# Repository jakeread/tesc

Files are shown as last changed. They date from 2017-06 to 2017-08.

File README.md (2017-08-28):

# FOCT v0.3
### Field Oriented Control on a Teensy 3.2

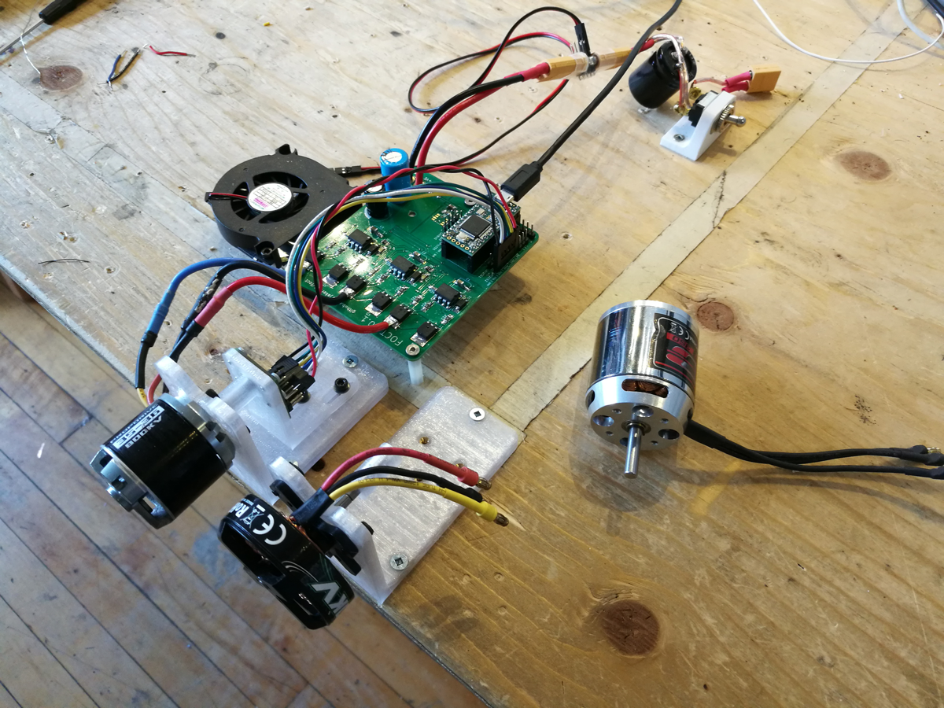
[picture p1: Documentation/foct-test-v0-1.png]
FOCT System


## Briefly
FOCT does closed-loop control of brushless dc (BLDC) motors: the type normally found in RC Cars, Airplanes, Drones etc. These motors are incredibly power-dense, making them an excellent candidate for Robotics applications. However, it's very difficult to control them at low speeds and in small position intervals. 

FOCT implements 'all the bells and whistles' found in high-end robotics motor controllers (encoder feedback, BEMF & current sensing, etc) in a relatively low-cost solution. Code is written in Arduino for the Teensy Microcontroller, and is meant to be easily extensible and pick-through-able.

FOCT is in development! So is it's documentation!

## The Hardware  
FOCT uses a Teensy 3.2 to control Three H-Bridges, which each drive one phase of a three-phase brushless motor. The H-Bridge gates are driven with a DRV8302, a wunderkid IC that is also home to a 5V Buck Converter (for your peripheral needs) and two differential Op-Amps, used to measure phase current. The board also has simple voltage-dividers connected to Teensy ADCs for measuring phase voltage, and includes an SPI out connector used to interface with an AS5047 encoder for absolute position sensing. For now, input is done over Teensy's blazing-fast serial port.  
  
Up to ~24v supply  
Up to 30A without a heatsink, 42 with good cooling, peaks of 60  
Planned PWM in, SPI slave modes for control. Serial over USB Config / testing.  

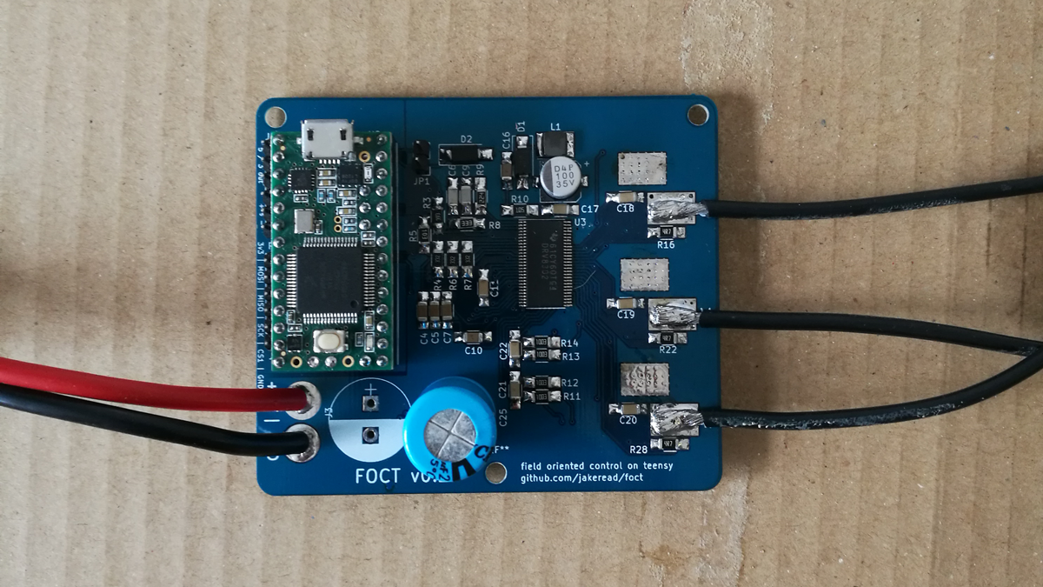
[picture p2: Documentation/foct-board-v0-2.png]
FOCT v0.2 Hardware


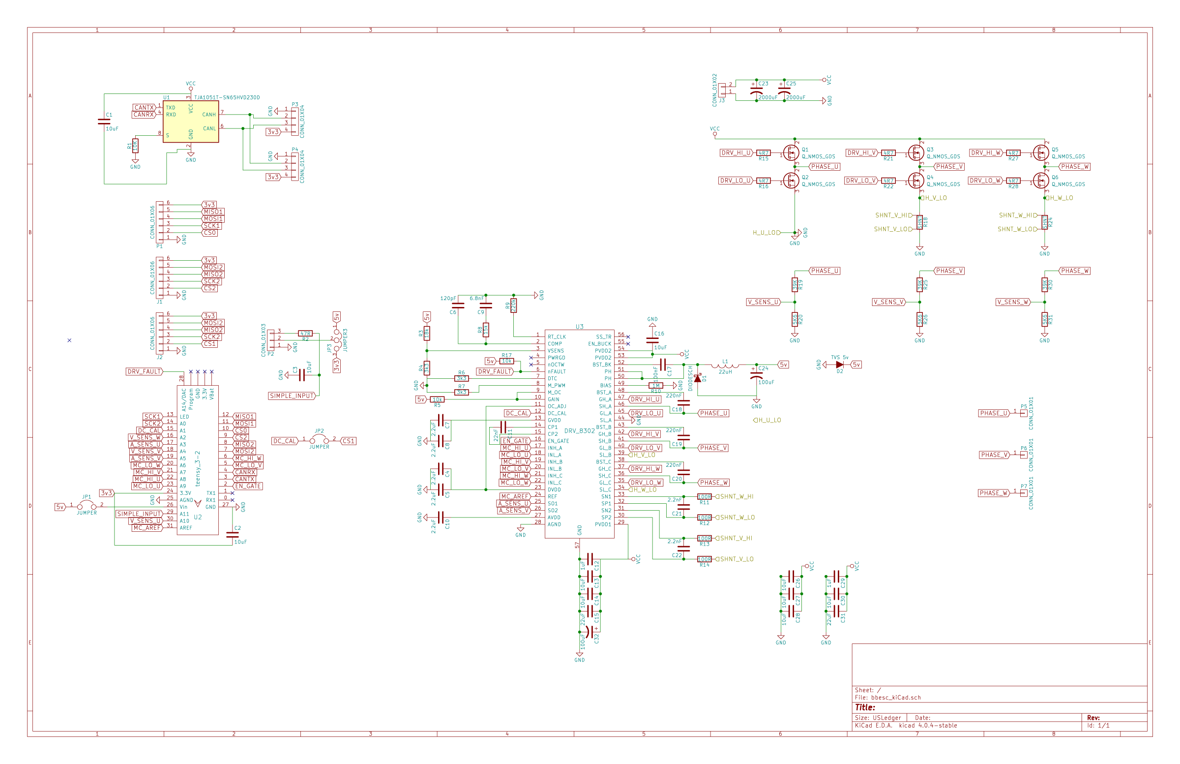
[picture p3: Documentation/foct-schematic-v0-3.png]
FOCT v0.3 Schematic


## The Software
FOCT runs on Arduino! It uses Teensy's built interval timers to handle fast-loop-insurance, and only occasionally reaches into the chip's registers to make PWM work properly. Code will be well commented, I hope / promise...

## How it Works: Closed-Loop BLDC Control
// 6-step commutation w/ position reference

## How it Works: Field-Oriented Control
// FOC ! Transforms, current measurement, UVW || AB || IQ frames  

## TBD's, software
- Proper filtering on Current measurement, encoder measurement  
- Tuning the FOC loop  
- Encoder Offset Discovery routine  
- Auto Tuning, interface, system integration, oh my

## TBD's, hardware
- ADC voltage divider to sense VBUS voltage
- More DAC outputs / testing pins so to tune FOC
- SMD Thermistor near the FETS ?  
- Go to STM32F4 & chibios ?
- Caps could be closer to FETS, heatsink strap

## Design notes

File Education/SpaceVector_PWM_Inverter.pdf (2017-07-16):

## PROJECT #2 SPACE VECTOR PWM INVERTER

JIN-WOO JUNG, PH.D STUDENT

E-mail: jung.103@osu.edu
Tel.: (614) 292-3633

ADVISOR: PROF. ALI KEYHANI

## DATE: FEBRUARY 20, 2005

### MECHATRONIC SYSTEMS LABORATORY

### DEPARTMENT OF ELECTRICAL AND COMPUTER ENGINEERING

### THE OHIO STATE UNIVERSITY

### 1. Problem Description

In this simulation, we will study Space Vector Pulse Width Modulation (SVPWM) technique. We will use the SEMIKRON® IGBT Flexible Power Converter for this purpose. The system configuration is given below:

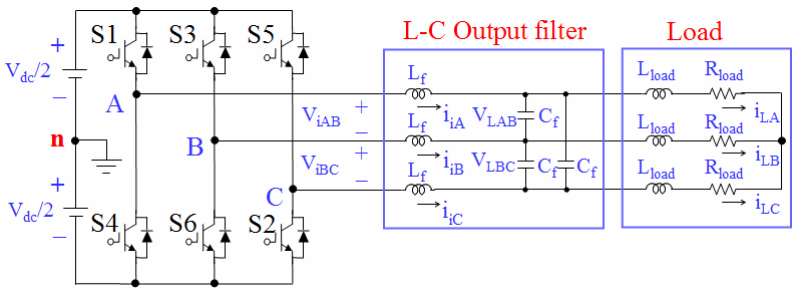
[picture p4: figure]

Fig. 1 Circuit model of three-phase PWM inverter with a center-taped grounded DC bus.

The system parameters for this converter are as follows:

IGBTs: SEMIKRON SKM 50 GB 123D, Max ratings: VCES = 600 V, IC = 80 A DC- link voltage: Vdc = 400 V
Fundamental frequency: f = 60 Hz
PWM (carrier) frequency: fz = 3 kHz
Modulation index: a = 0.6
Output filter: Lf = 800 µH and Cf = 400 µF
Load: Lload = 2 mH and Rload = 5 Ω

Using Matlab/Simulink, simulate the circuit model described in Fig. 1 and plot the waveforms of Vi (= [ViAB ViBC ViCA]), Ii (= [iiA iiB iiC]), VL (= [VLAB VLBC VLCA]), and IL (= [iLA iLB iLC]).

### 2. Space Vector PWM

### 2.1 Principle of Pulse Width Modulation (PWM)

Fig. 2 shows circuit model of a single-phase inverter with a center-taped grounded DC bus, and Fig 3 illustrates principle of pulse width modulation.

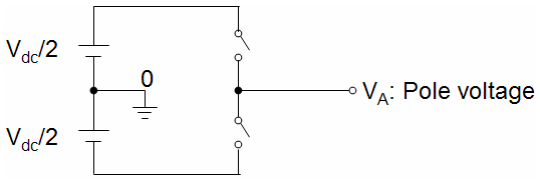
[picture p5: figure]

Fig. 2 Circuit model of a single-phase inverter.

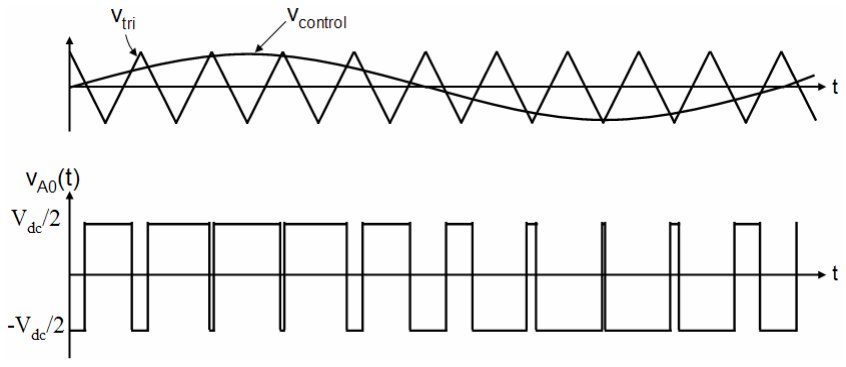
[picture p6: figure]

Fig. 3 Pulse width modulation.

As depicted in Fig. 3, the inverter output voltage is determined in the following: When Vcontrol > Vtri, VA0 = Vdc/2
When Vcontrol < Vtri, VA0 = −Vdc/2

Also, the inverter output voltage has the following features:
PWM frequency is the same as the frequency of Vtri
Amplitude is controlled by the peak value of Vcontrol
Fundamental frequency is controlled by the frequency of Vcontrol

Modulation index (m) is defined as:

A0 1 | A0 0 1

where, (V ) : fundamental frequecny component of V

, / 2

( )

dc

A

tri

control
V

peak of V
v

v
∴m = =

### 2.2 Principle of Space Vector PWM

The circuit model of a typical three-phase voltage source PWM inverter is shown in Fig. 4. S1 to S6 are the six power switches that shape the output, which are controlled by the switching variables a, a′, b, b′, c and c′. When an upper transistor is switched on, i.e., when a, b or c is 1, the corresponding lower transistor is switched off, i.e., the corresponding a′, b′ or c′ is 0. Therefore, the on and off states of the upper transistors S1, S3 and S5 can be used to determine the output voltage.

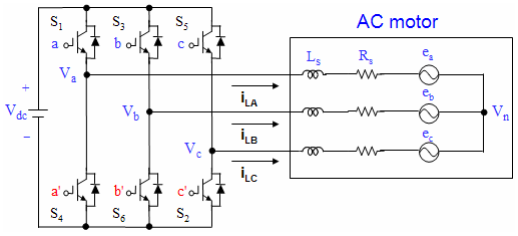
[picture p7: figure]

Fig. 4 Three-phase voltage source PWM Inverter.

The relationship between the switching variable vector [a, b, c]t and the line-to-line voltage vector [Vab Vbc Vca]

t
is given by (2.1) in the following:

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
1 0 | 1
0 | 1 | 1
1 | 1 0
. | (2.1)

Also, the relationship between the switching variable vector [a, b, c]t and the phase voltage
vector [Va Vb Vc]

t
can be expressed below.

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
− − − −
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
1 | 1 2
1 2 | 1
2 | 1 | 1
3 | . | (2.2)

As illustrated in Fig. 4, there are eight possible combinations of on and off patterns for the three upper power switches. The on and off states of the lower power devices are opposite to the upper one and so are easily determined once the states of the upper power transistors are determined. According to equations (2.1) and (2.2), the eight switching vectors, output line to neutral voltage (phase voltage), and output line-to-line voltages in terms of DC-link Vdc, are given in Table1 and Fig. 5 shows the eight inverter voltage vectors (V0 to V7).

Table 1. Switching vectors, phase voltages and output line to line voltages

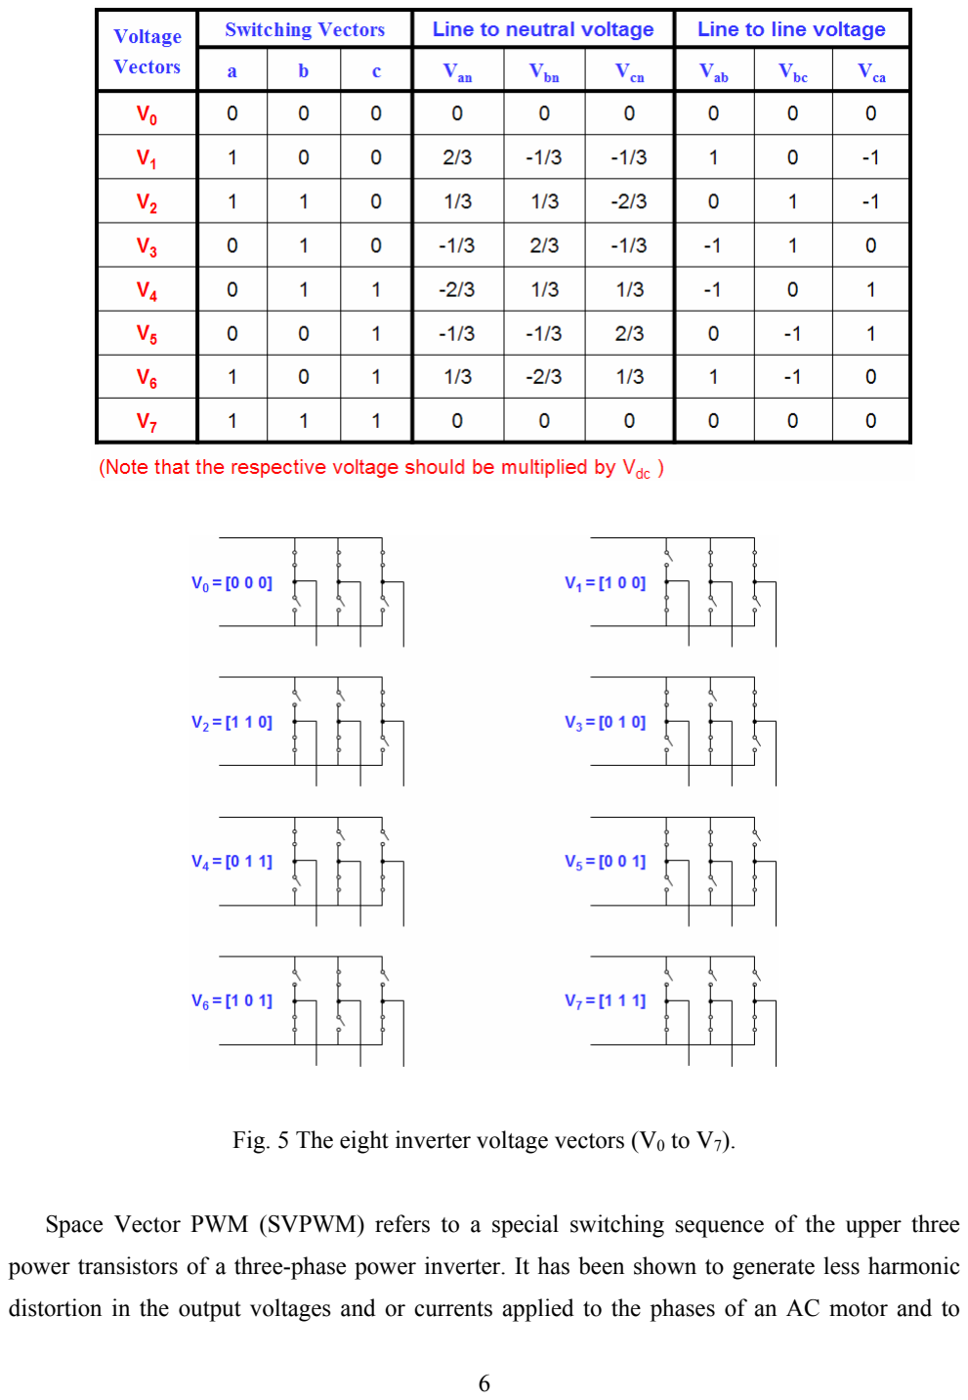
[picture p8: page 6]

Fig. 5 The eight inverter voltage vectors (V0 to V7).

Space Vector PWM (SVPWM) refers to a special switching sequence of the upper three power transistors of a three-phase power inverter. It has been shown to generate less harmonic distortion in the output voltages and or currents applied to the phases of an AC motor and to provide more efficient use of supply voltage compared with sinusoidal modulation technique as shown in Fig. 6.

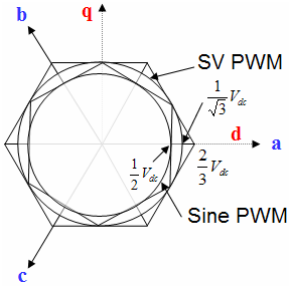
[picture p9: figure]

Fig. 6 Locus comparison of maximum linear control voltage in Sine PWM and SVPWM.

To implement the space vector PWM, the voltage equations in the abc reference frame

can be transformed into the stationary dq reference frame that consists of the horizontal (d) and

vertical (q) axes as depicted in Fig. 7.

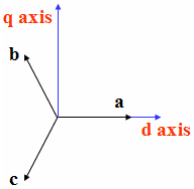
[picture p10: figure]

Fig. 7 The relationship of abc reference frame and stationary dq reference frame.

From this figure, the relation between these two reference frames is below

dq | s abc f | = K f 0 | (2.3)

where,
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
1/ 2 1/ 2 | 1/ 2
0 | 3 2 | 3 2
1 | 1/ 2 | 1/ 2

3

2 Ks | , fdq0=[fd fq f0]
T
, fabc=[fa fb fc]

T
, and f denotes either a voltage

or a current variable.

As described in Fig. 7, this transformation is equivalent to an orthogonal projection of [a, b, c]t

onto the two-dimensional perpendicular to the vector [1, 1, 1]t
(the equivalent d-q plane) in a three-dimensional coordinate system. As a result, six non-zero vectors and two zero vectors are possible. Six nonzero vectors (V1 - V6) shape the axes of a hexagonal as depicted in Fig. 8, and feed electric power to the load. The angle between any adjacent two non-zero vectors is 60 degrees. Meanwhile, two zero vectors (V0 and V7) are at the origin and apply zero voltage to the load. The eight vectors are called the basic space vectors and are denoted by V0, V1, V2, V3, V4,

V5, V6, and V7. The same transformation can be applied to the desired output voltage to get the desired reference voltage vector Vref in the d-q plane.
The objective of space vector PWM technique is to approximate the reference voltage vector Vref using the eight switching patterns. One simple method of approximation is to generate the average output of the inverter in a small period, T to be the same as that of Vref in the same period.

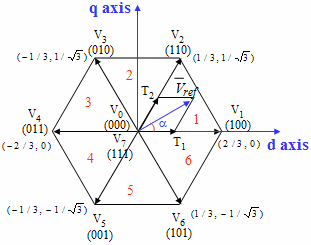
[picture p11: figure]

Fig. 8 Basic switching vectors and sectors.

Therefore, space vector PWM can be implemented by the following steps:

Step 1. Determine Vd, Vq, Vref, and angle (α)
Step 2. Determine time duration T1, T2, T0
Step 3. Determine the switching time of each transistor (S1 to S6)

### 2.2.1 Step 1: Determine Vd, Vq, Vref, and angle (α)

From Fig. 9, the Vd, Vq, Vref, and angle (α) can be determined as follows:

an | bn | cn
d | an | bn | cn
V
2

1 V
2

1 V

V | V | V | cos60 V cos60
= | − | −
= | − | ⋅ | − | ⋅
an | bn | cn
q | bn | cn
V
2

3 V
2

3 V

V | 0 V | cos30 V cos30
= | + | −
= + | ⋅ | − | ⋅

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
2 | 2 ∴ Vref = Vd +Vq
tan | 2 , where f fundamental frequency ¹ | = | = | = ⎟

⎟
⎠

⎞
⎜

⎜
⎝

⎛
∴ = | − | t | ft V

V

d

q α | ω π

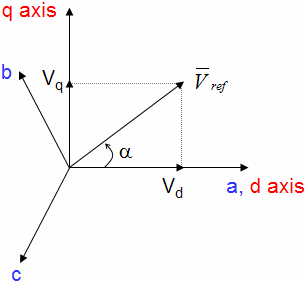
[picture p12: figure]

Fig. 9 Voltage Space Vector and its components in (d, q).

### 2.2.2 Step 2: Determine time duration T1, T2, T0

From Fig. 10, the switching time duration can be calculated as follows:

Switching time duration at Sector 1

(where, 0 α 60 )

sin ( / 3)

cos( / 3) V
3

2 T
0

1
V
3

2 T
sin ( )
cos( ) T | V
T V | (T V | T V )
V | V dt | V dt | V
1 | dc | 2 | dc ref z
z | ref | 1 | 1 | 2 | 2

Tz

| | | | | T1 T2

0

T1 T2

T1

2

Tz

0

T1

0

ref | 1

≤ ≤ °

⎥
⎦

⎤ ⎢
⎣

⎡
+ ⋅ ⋅ ⋅ ⎥
⎦

⎤
⎢
⎣

⎡ = ⋅ ⋅ ⋅ ⎥
⎦

⎤ ⎢
⎣

⎡
⇒ ⋅ | ⋅
∴ ⋅ | = | ⋅ | + ⋅
= | + | + ∫ | ∫ | ∫ | ∫

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
∴ = − | + | = | =

∴ = ⋅ ⋅

− ∴ = ⋅ ⋅

dc

ref

z

0 | 1 | 2 | z

2

1

V
3

2

V
and a
f
1 ( | ), | where, T

sin ( / 3)

sin ( )

sin ( / 3)

sin ( / 3 | )
T | T | T T
T | T a

T T a

z

z

z

π

α

π

π α

Switching time duration at any Sector

⎟

⎟
⎠

⎞

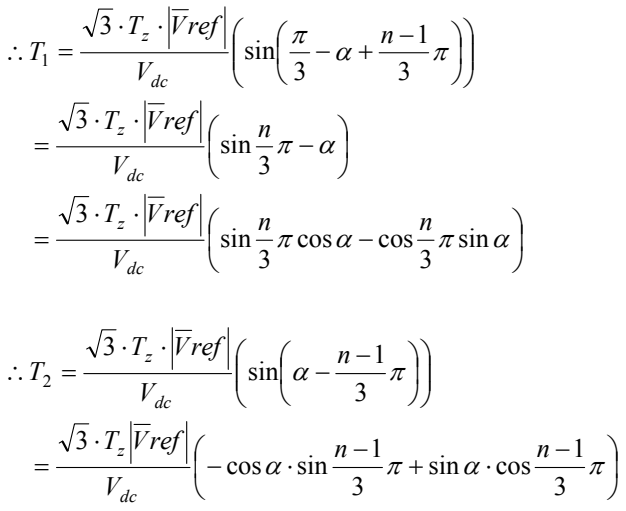
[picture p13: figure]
1 sin; cos; cos sin; sin; T Vref

⎜

⎜
⎝

⎛
≤ ≤ °

= ∴ = − −
0 α 60

where, n 1 through 6(that is,Sector1 to 6) ,
0 | 1 | 2
T | T T T z

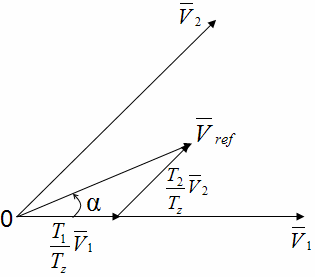
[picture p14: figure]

Fig. 10 Reference vector as a combination of adjacent vectors at sector 1.

### 2.2.3 Step 3: Determine the switching time of each transistor (S1 to S6)

Fig. 11 shows space vector PWM switching patterns at each sector.

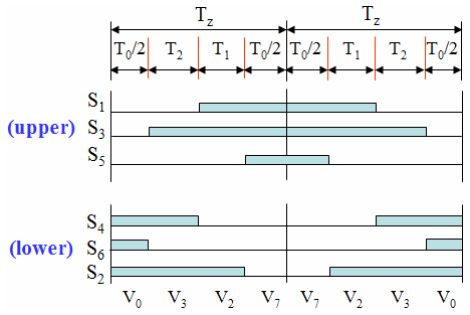
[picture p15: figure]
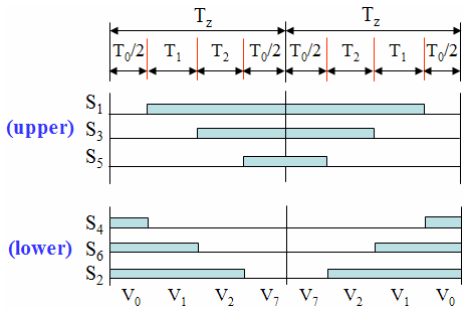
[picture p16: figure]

(a) Sector 1. | (b) Sector 2.

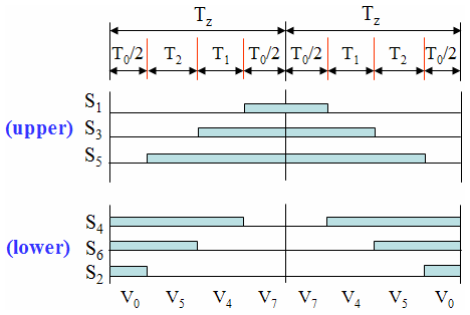
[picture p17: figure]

(c) Sector 3. | (d) Sector 4.

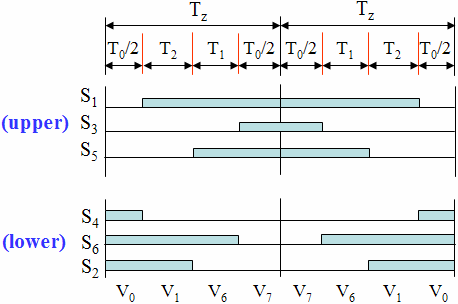
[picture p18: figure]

(e) Sector 5. | (f) Sector 6.

Fig. 11 Space Vector PWM switching patterns at each sector.

Based on Fig. 11, the switching time at each sector is summarized in Table 2, and it will be built in Simulink model to implement SVPWM.

Table 2. Switching Time Calculation at Each Sector

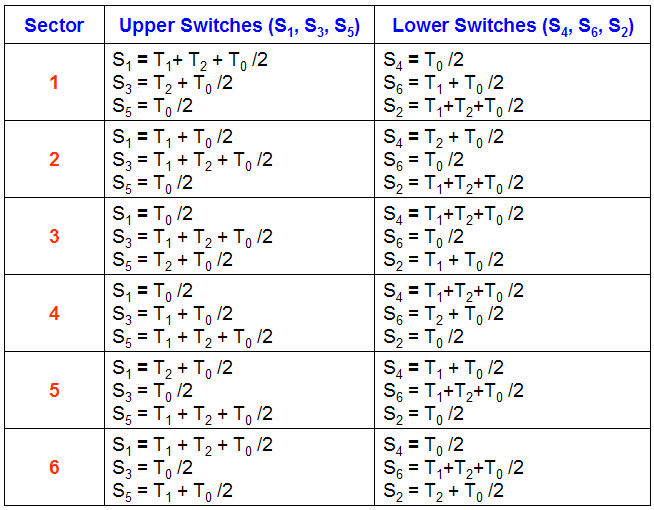
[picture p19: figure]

### 3. State-Space Model

Fig. 12 shows L-C output filter to obtain current and voltage equations.

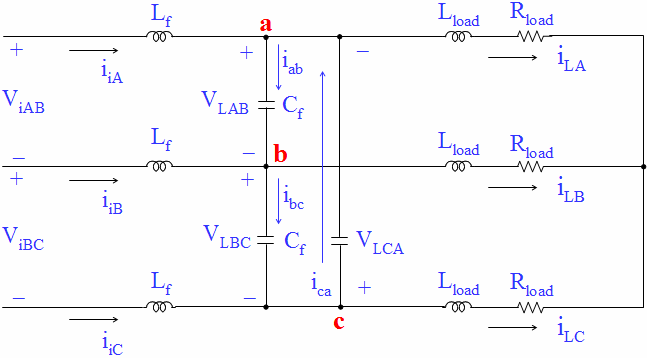
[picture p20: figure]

Fig. 12 L-C output filter for current/voltage equations.

By applying Kirchoff’s current law to nodes a, b, and c, respectively, the following current equations are derived:

c node “a”:

LA

LAB
f

LCA
iA | ca | ab | LA | iA | f | i
dt

dV C
dt

dV
i + i = i + i | ⇒ i + C | = | + . | (3.1)

d node “b”:

LB

LBC
f

LAB
iB | ab | bc | LB | iB | f | i
dt

dV C
dt

dV
i + i = i + i | ⇒ i + C | = | + . | (3.2)

e node “c”:

LC

LCA
f

LBC
iC | bc | ca | LC | iC | f | i
dt

dV C
dt

dV
i + i = i + i | ⇒ i + C | = | + | . | (3.2)
where, | , | , | . dt
| dV
i | C
dt

dV
i C
dt

dV
i | C | LCA
ca | f

LBC
bc | f

LAB

ab = f | = | =

Also, (3.1) to (3.3) can be rewritten as the following equations, respectively:

c subtracting (3.2) from (3.1):

iA | iB | LA | LB
LCA | LBC | LAB
f
LA | LB
LAB | LBC
f
LCA | LAB
iA | iB | f
i | i | i | i
dt

dV
dt

dV
dt

dV C

i i
dt

dV
dt

dV C
dt

dV
dt

dV
i | i | C
⎟ = − + + | − ⎠

⎞ ⎜
⎝

⎛
⇒ | + | − ⋅
⎟ + | − ⎠

⎞ ⎜
⎝
⎛ ⎟ = | − ⎠

⎞ ⎜
⎝
⎛ − + | −

2

. (3.4)

d subtracting (3.3) from (3.2):

iB | iC | LB | LC
LAB | LCA | LBC
f
LB | LC
LBC | LCA
f
LAB | LBC
iB | iC | f
i | i | i | i
dt

dV
dt

dV
dt

dV C

i i
dt

dV
dt

dV C
dt

dV
dt

dV
i | i | C
⎟ = − + + | − ⎠

⎞ ⎜
⎝

⎛
⇒ | + | − ⋅
⎟ + | − ⎠

⎞ ⎜
⎝
⎛ ⎟ = | − ⎠

⎞ ⎜
⎝
⎛ − + | −

2

. (3.5)

e subtracting (3.1) from (3.3):

iC | iA | LC | LA
LAB | LBC | LCA
f
LC | LA
LCA | LAB
f
LBC | LCA
iC | iA | f
i | i | i | i
dt

dV
dt

dV
dt

dV C

i i
dt

dV
dt

dV C
dt

dV
dt

dV
i | i | C
⎟ = − + + | − ⎠

⎞ ⎜
⎝

⎛
⇒ | + | − ⋅
⎟ + | − ⎠

⎞ ⎜
⎝
⎛ ⎟ = | − ⎠

⎞ ⎜
⎝
⎛ − + | −

2

. (3.6)

To simplify (3.4) to (3.6), we use the following relationship that an algebraic sum of line to line load voltages is equal to zero:

VLAB + VLBC + VLCA = 0. | (3.7)

Based on (3.7), the (3.4) to (3.6) can be modified to a first-order differential equation, respectively:

()
()

() ⎪

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
= | −
= | −
= | −

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
dt C

dV

i
C

i
dt C

dV

i
C

i
dt C

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
, | (3.8)

where, iiAB = iiA ─ iiB, iiBC = iiB ─ iiC, iiCA = iiC ─ iiA and iLAB = iLA ─ iLB, iLBC = iLB ─ iLC,

iLCA = iLC ─ iLA.

By applying Kirchoff’s voltage law on the side of inverter output, the following voltage equations can be derived:

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
= − | +
= − | +
= − | +

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
dt L

di

V
L

V
dt L

di

V
L

V
dt L

di

1 | 1
1 | 1
1 | 1
. | (3.9)

By applying Kirchoff’s voltage law on the load side, the following voltage equations can be derived:

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
= | + | − | −
= | + | − | −
= | + | − | −

load LA

LA
load LC load

LC
LCA load

load LC

LC
load LB load

LB
LBC load

load LB

LB
load LA load

LA
LAB load

R i
dt

di R i L
dt

di
V L

R i
dt

di
R i L
dt

di V L

R i
dt

di R i L
dt
di V | L
. | (3.10)

Equation (3.10) can be rewritten as:

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
= − | +
= − | +
= − | +

LCA
load

LCA
load
LCA | load

LBC
load

LBC
load
LBC | load

LAB
load

LAB
load
LAB | load

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
. | (3.11)

Therefore, we can rewrite (3.8), (3.9) and (3.11) into a matrix form, respectively:

L
load

load
L
load

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
dt L

d

dt | L | L

d

dt | C | C

d

V I I

V V I

I I V

= | −
= − | +
= | −

1

1 1

3

1
3

1

, | (3.12)

where, VL = [VLAB VLBC VLCA]

T
, Ii = [iiAB iiBC iiCA]

T = [iiA-iiB iiB-iiC iiC-iiA]

T
, Vi = [ViAB ViBC ViCA]

T
,

IL = = [iLAB iLBC iLCA]

T = [iLA-iLB iLB-iLC iLC-iLA]

T

Finally, the given plant model (3.12) can be expressed as the following continuous-time state space equation

X(t) = AX(t) + Bu(t) & | , | (3.13)

where,

9×1 ⎥

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
3 3 | 3 3 | 3 3
3 3 | 3 3 | 3 3
3 3 | 3 3 | 3 3

0 1

0 | 0 1

3

1
3

1 0

×

× | × | ×
× | × | ×
× | × | ×

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
load

load

load

f

f | f
A ,

3 3 9 3

3 3

3 3

0

1

0

× | ×

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
B | , | [ ]3×1 u = Vi | .

Note that load line to line voltage VL, inverter output current Ii, and the load current IL are the state variables of the system, and the inverter output line-to-line voltage Vi is the control input (u).

### 4. Simulation Steps

1). Initialize system parameters using Matlab

2). Build Simulink Model
Determine sector
Determine time duration T1, T2, T0
Determine the switching time (Ta, Tb, and Tc) of each transistor (S1 to S6)
Generate the inverter output voltages (ViAB, ViBC, ViCA,) for control input (u) Send data to Workspace

3). Plot simulation results using Matlab

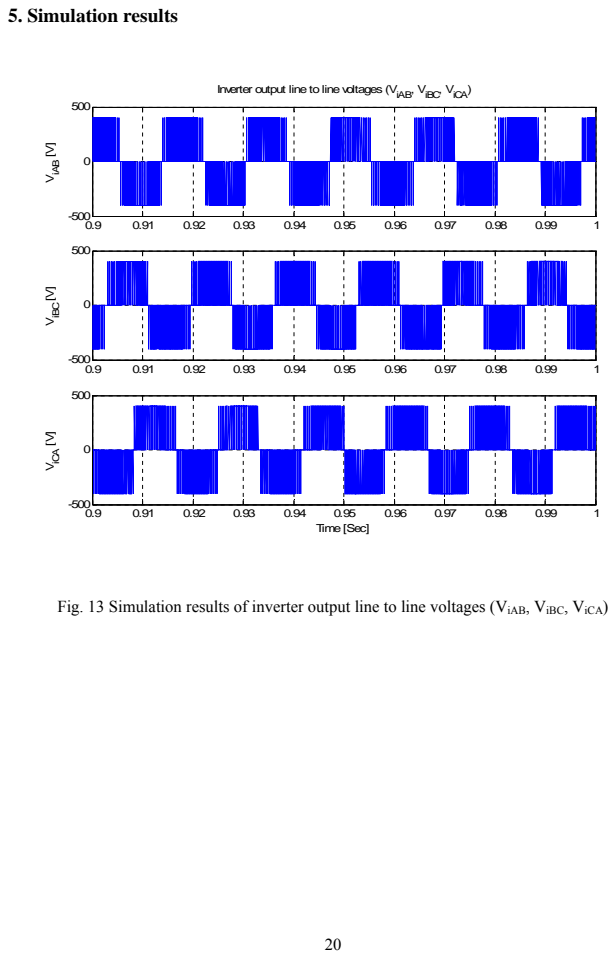
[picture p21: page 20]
5. Simulation results; ViAB [V]; ViBC [V]; ViCA [V]; Time [Sec]

Inverter output line to line voltages (ViAB, ViBC, ViCA)

Fig. 13 Simulation results of inverter output line to line voltages (ViAB, ViBC, ViCA)

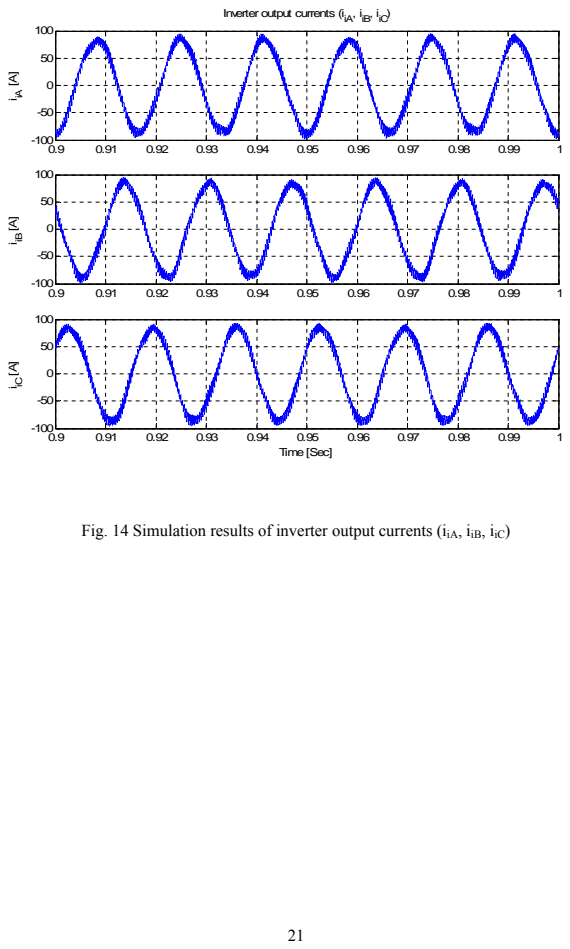
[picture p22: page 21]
iiA [A]; iiB [A]; iiC [A]; Time [Sec]

Inverter output currents (iiA, iiB, iiC)

Fig. 14 Simulation results of inverter output currents (iiA, iiB, iiC)

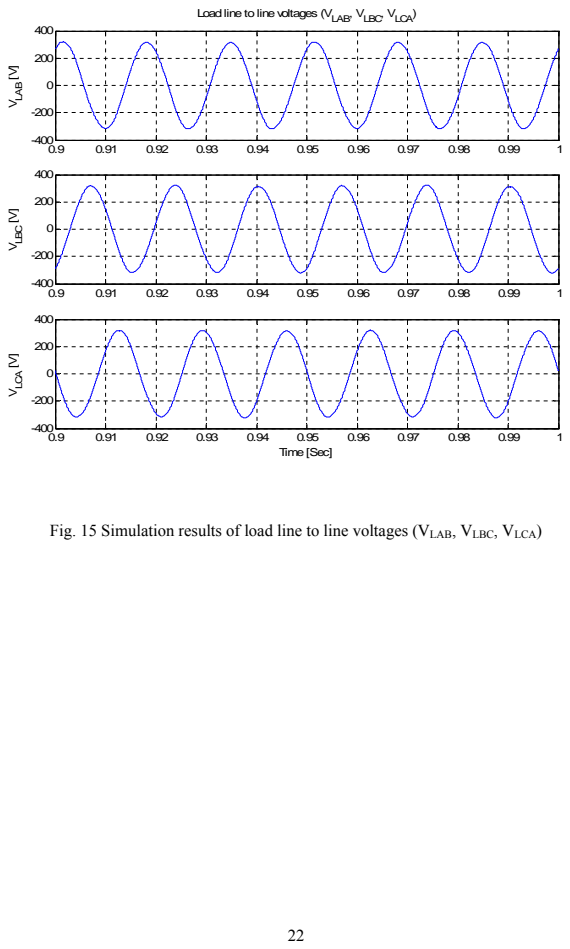
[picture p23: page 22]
VLAB [V]; VLBC [V]; VLCA [V]; Time [Sec]

Load line to line voltages (VLAB, VLBC, VLCA)

Fig. 15 Simulation results of load line to line voltages (VLAB, VLBC, VLCA)

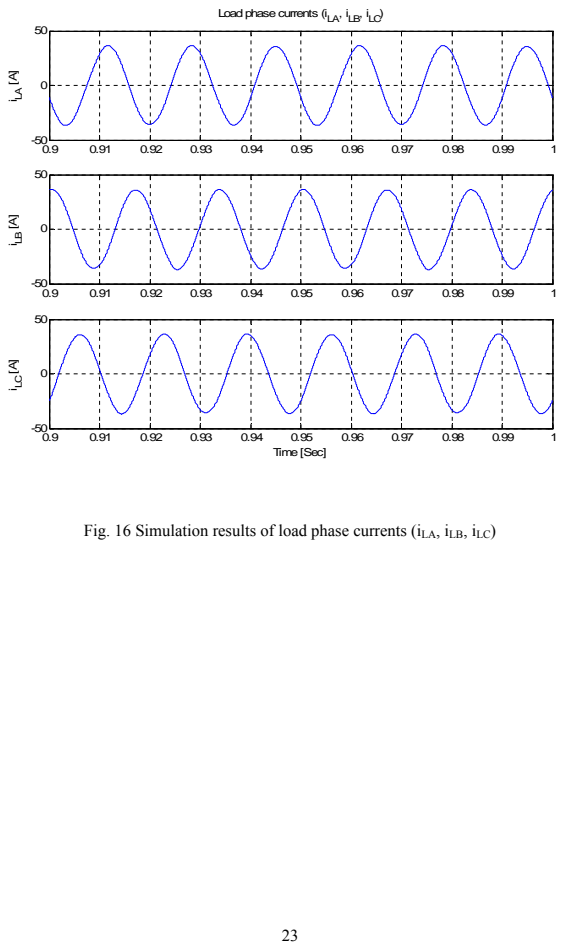
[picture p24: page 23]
iLA [A]; iLB [A]; iLC [A]; Time [Sec]

Load phase currents (iLA, iLB, iLC)

Fig. 16 Simulation results of load phase currents (iLA, iLB, iLC)

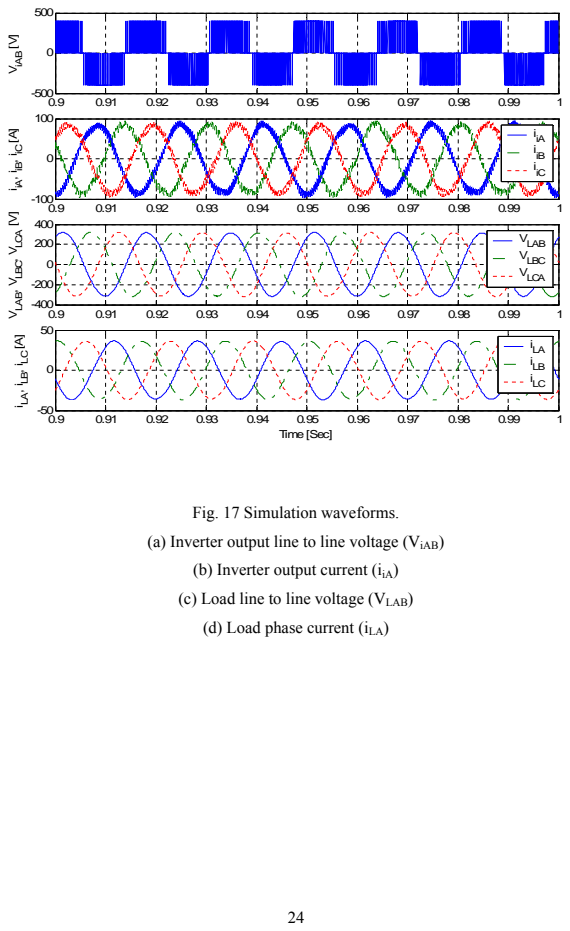
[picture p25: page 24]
ViAB [V]; Time [Sec]

iiA, iiB, iiC [A]

VLAB, VLBC, VLCA [V]

VLAB
VLBC
VLCA

iLA, iLB, iLC [A]

Fig. 17 Simulation waveforms.
(a) Inverter output line to line voltage (ViAB)
(b) Inverter output current (iiA)
(c) Load line to line voltage (VLAB)
(d) Load phase current (iLA)

## Appendix

Matlab/Simulink Codes

A.1 Matlab Code for System Parameters
% Written by Jin Woo Jung
% Date: 02/20/05
% ECE743, Simulation Project #2 (Space Vector PWM Inverter) % Matlab program for Parameter Initialization

clear all % clear workspace

% Input data
Vdc= 400; % DC-link voltage
Lf= 800e-6;% Inductance for output filter Cf= 400e-6; % Capacitance for output filter Lload = 2e-3; %Load inductance
Rload= 5; % Load resistance
f= 60; % Fundamental frequency
fz = 3e3; % Switching frequency a= 0.6;% Modulation index
w= 2*pi*60; %angular frequency
Tz= 1/fz; % Sampling time
V_ref= (2/3)*a*Vdc; % Reference voltage

% Coefficients for State-Space Model
A=[zeros(3,3) eye(3)/(3*Cf) -eye(3)/(3*Cf)
-eye(3)/Lf | zeros(3,3) | zeros(3,3)
eye(3,3)/Lload zeros(3,3) -eye(3)*Rload/Lload]; % system matrix

B=[zeros(3,3)
eye(3)/Lf
zeros(3,3)]; % coefficient for the control variable u

C=[eye(9)]; % coefficient for the output y

D=[zeros(9,3)]; % coefficient for the output y

Ks = 1/3*[-1 0 1; 1 -1 0; 0 1 -1]; % Conversion matrix to transform [iiAB iiBC iiCA] to [iiA iiB iiC]

A.2 Matlab Code for Plotting the Simulation Results % Written by Jin Woo Jung
% Date: 02/20/05
% ECE743, Simulation Project #2 (Space Vector PWM)

% Matlab program for plotting Simulation Results
% using Simulink

ViAB = Vi(:,1);
ViBC = Vi(:,2);
ViCA = Vi(:,3);

VLAB= VL(:,1);
VLBC= VL(:,2);
VLCA= VL(:,3);

iiA= IiABC(:,1);
iiB= IiABC(:,2);
iiC= IiABC(:,3);

iLA= ILABC(:,1);
iLB= ILABC(:,2);
iLC= ILABC(:,3);

figure(1)
subplot(3,1,1)
plot(t,ViAB)
axis([0.9 1 -500 500])
ylabel('V_i_A_B [V]')
title('Inverter output line to line voltages (V_i_A_B, V_i_B_C, V_i_C_A)')

grid

subplot(3,1,2)
plot(t,ViBC)
axis([0.9 1 -500 500])
ylabel('V_i_B_C [V]')
grid

subplot(3,1,3)
plot(t,ViCA)
axis([0.9 1 -500 500])
ylabel('V_i_C_A [V]')
xlabel('Time [Sec]')
grid

figure(2)
subplot(3,1,1)
plot(t,iiA)
axis([0.9 1 -100 100])
ylabel('i_i_A [A]')
title('Inverter output currents (i_i_A, i_i_B, i_i_C)') grid

subplot(3,1,2)
plot(t,iiB)
axis([0.9 1 -100 100])
ylabel('i_i_B [A]')
grid

subplot(3,1,3)

plot(t,iiC)
axis([0.9 1 -100 100])
ylabel('i_i_C [A]')
xlabel('Time [Sec]')
grid

figure(3)
subplot(3,1,1)
plot(t,VLAB)
axis([0.9 1 -400 400])
ylabel('V_L_A_B [V]')
title('Load line to line voltages (V_L_A_B, V_L_B_C, V_L_C_A)') grid

subplot(3,1,2)
plot(t,VLBC)
axis([0.9 1 -400 400])
ylabel('V_L_B_C [V]')
grid

subplot(3,1,3)
plot(t,VLCA)
axis([0.9 1 -400 400])
ylabel('V_L_C_A [V]')
xlabel('Time [Sec]')
grid

figure(4)
subplot(3,1,1)
plot(t,iLA)
axis([0.9 1 -50 50])

ylabel('i_L_A [A]')
title('Load phase currents (i_L_A, i_L_B, i_L_C)') grid

subplot(3,1,2)
plot(t,iLB)
axis([0.9 1 -50 50])
ylabel('i_L_B [A]')
grid

subplot(3,1,3)
plot(t,iLC)
axis([0.9 1 -50 50])
ylabel('i_L_C [A]')
xlabel('Time [Sec]')
grid

figure(5)
subplot(4,1,1)
plot(t,ViAB)
axis([0.9 1 -500 500])
ylabel('V_i_A_B [V]')
grid

subplot(4,1,2)
plot(t,iiA,'-', t,iiB,'-.',t,iiC,':') axis([0.9 1 -100 100])
ylabel('i_i_A, i_i_B, i_i_C [A]') legend('i_i_A', 'i_i_B', 'i_i_C') grid

subplot(4,1,3)
plot(t,VLAB,'-', t,VLBC,'-.',t,VLCA,':') axis([0.9 1 -400 400])
ylabel('V_L_A_B, V_L_B_C, V_L_C_A [V]') legend('V_L_A_B', 'V_L_B_C', 'V_L_C_A') grid

subplot(4,1,4)
plot(t,iLA,'-', t,iLB,'-.',t,iLC,':') axis([0.9 1 -50 50])
ylabel('i_L_A, i_L_B, i_L_C [A]') legend('i_L_A', 'i_L_B', 'i_L_C') xlabel('Time [Sec]')
grid

A.3 Simulink Code

Simulink Model for Overall System

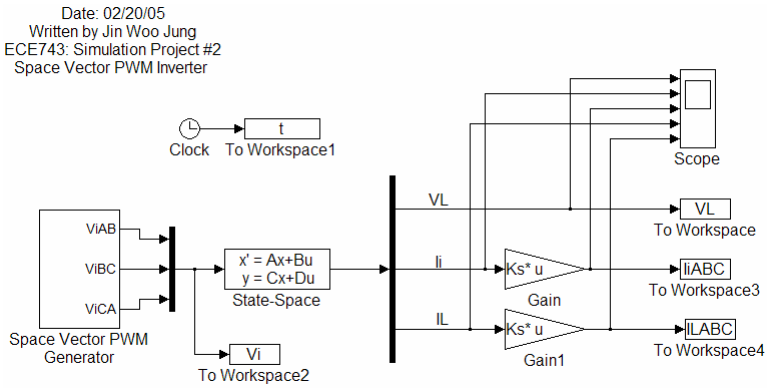
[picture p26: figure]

Subsystem Simulink Model for “Space Vector PWM Generator”

Subsystem Simulink Model for “Making Switching Time”

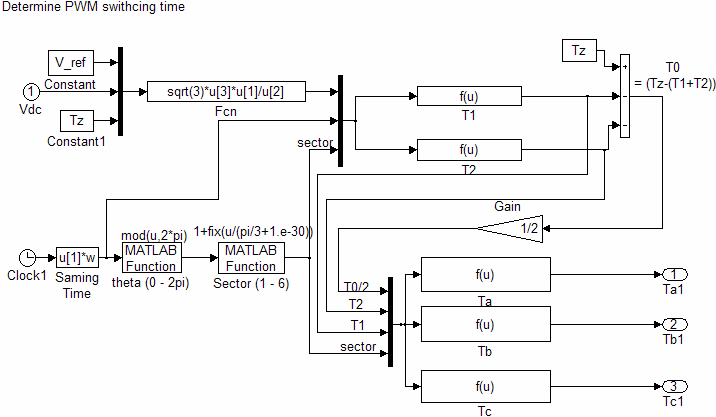
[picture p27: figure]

1). T1 = u[1]*(sin(u[3]*pi/3)*cos(u[2])-cos(u[3]*pi/3)*sin(u[2]))

2). T2 = u[1]*(cos((u[3]-1)*(pi/3))*sin(u[2])-sin((u[3]-1)*(pi/3))*cos(u[2]))

3). Ta = (u[4]==1)*(u[1]+u[2]+u[3])+(u[4]==2)*(u[1]+u[2]+u[3]) + (u[4]==3)*(u[1]+u[3]) + (u[4]==4)*(u[1])+ (u[4]==5)*(u[1])+ (u[4]==6)*(u[1]+u[2])

4). Tb = (u[4]==1)*(u[1])+(u[4]==2)*(u[1]+u[2]) + (u[4]==3)*(u[1]+u[2]+u[3]) + (u[4]==4)*(u[1]+u[2]+u[3])+ (u[4]==5)*(u[1]+u[3])+ (u[4]==6)*(u[1])

5). Tc = (u[4]==1)*(u[1]+u[3])+(u[4]==2)*(u[1]) + (u[4]==3)*(u[1]) + (u[4]==4)*(u[1]+u[2])+ (u[4]==5)*(u[1]+u[2]+u[3])+ (u[4]==6)*(u[1]+u[2]+u[3])

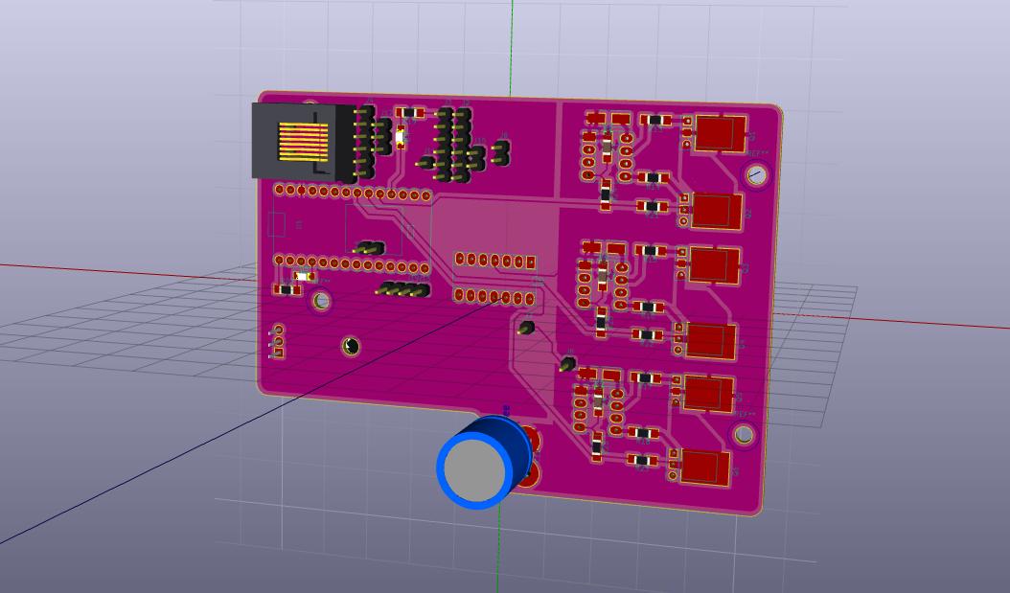
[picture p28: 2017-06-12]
Circuit/bbesc_kiCad.jpg

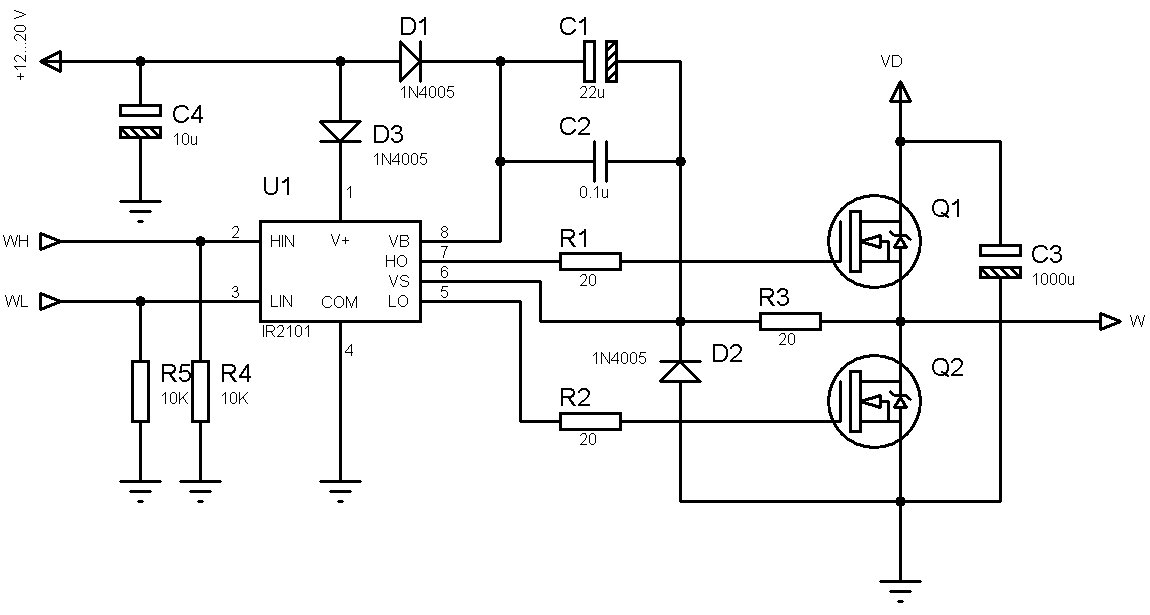
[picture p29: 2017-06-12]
Datasheets/Transistors and Drivers/IR2101-Circuit.png

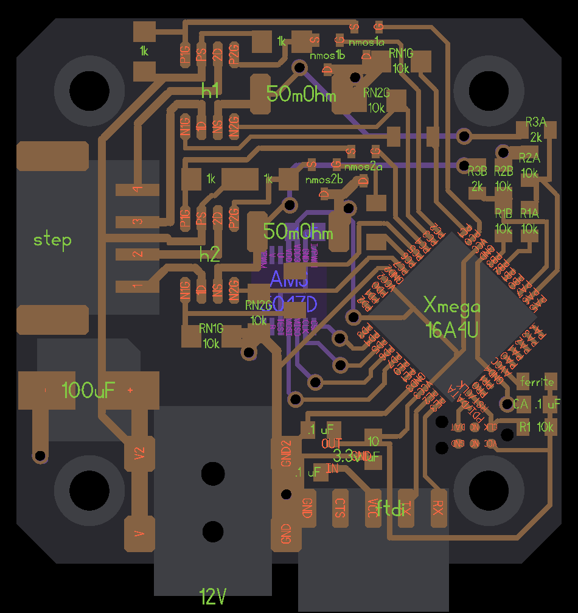
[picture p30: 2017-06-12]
Education/samServoStepper/servo-stepper-v1-layout.png

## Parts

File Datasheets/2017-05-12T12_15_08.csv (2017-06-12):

Index | Quantity | Part Number | Description | Customer Reference | Available Quantity | Backorder Quantity | Unit Price CAD | Extended Price CAD
1 | 3 | CSS2H-3920R-1L00FCT-ND | RES SMD 0.001 OHM 1% 8W 3920 |  | 3 | 0 | 2.61000 | 7.83
2 | 5 | ES1A-FDICT-ND | DIODE GEN PURP 50V 1A SMA |  | 5 | 0 | 0.73000 | 3.65
3 | 20 | 587-1352-1-ND | CAP CER 10UF 35V Y5V 1206 |  | 20 | 0 | 0.24500 | 4.90
4 | 2 | P14933-ND | CAP ALUM 2000UF 20% 35V RADIAL |  | 2 | 0 | 4.89000 | 9.78
5 | 10 | 516-1440-1-ND | LED RED DIFFUSED 1206 SMD |  | 10 | 0 | 0.58200 | 5.82
6 | 10 | 67-1002-1-ND | LED GREEN DIFFUSED 1206 SMD |  | 10 | 0 | 0.46600 | 4.66
7 | 10 | 516-1442-1-ND | LED YELLOW DIFFUSED 1206 SMD |  | 10 | 0 | 0.58200 | 5.82
8 | 20 | 311-1963-1-ND | CAP CER 1UF 50V X7R 1206 |  | 20 | 0 | 0.22500 | 4.50
9 | 20 | 311-1179-1-ND | CAP CER 0.1UF 50V X7R 1206 |  | 20 | 0 | 0.12900 | 2.58
10 | 10 | IRFU7440PBF-ND | MOSFET N CH 40V 90A I-PAK |  | 10 | 0 | 2.66900 | 26.69
11 | 3 | LM358NGOS-ND | IC OPAMP GP 1MHZ 8DIP |  | 3 | 0 | 0.66000 | 1.98
12 | 3 | IR2101PBF-ND | IC DRIVER HIGH/LOW SIDE 8DIP |  | 3 | 0 | 3.30000 | 9.90
13 | 2 | 497-1443-5-ND | IC REG LDO 5V 1.5A TO220AB |  | 2 | 0 | 0.69000 | 1.38

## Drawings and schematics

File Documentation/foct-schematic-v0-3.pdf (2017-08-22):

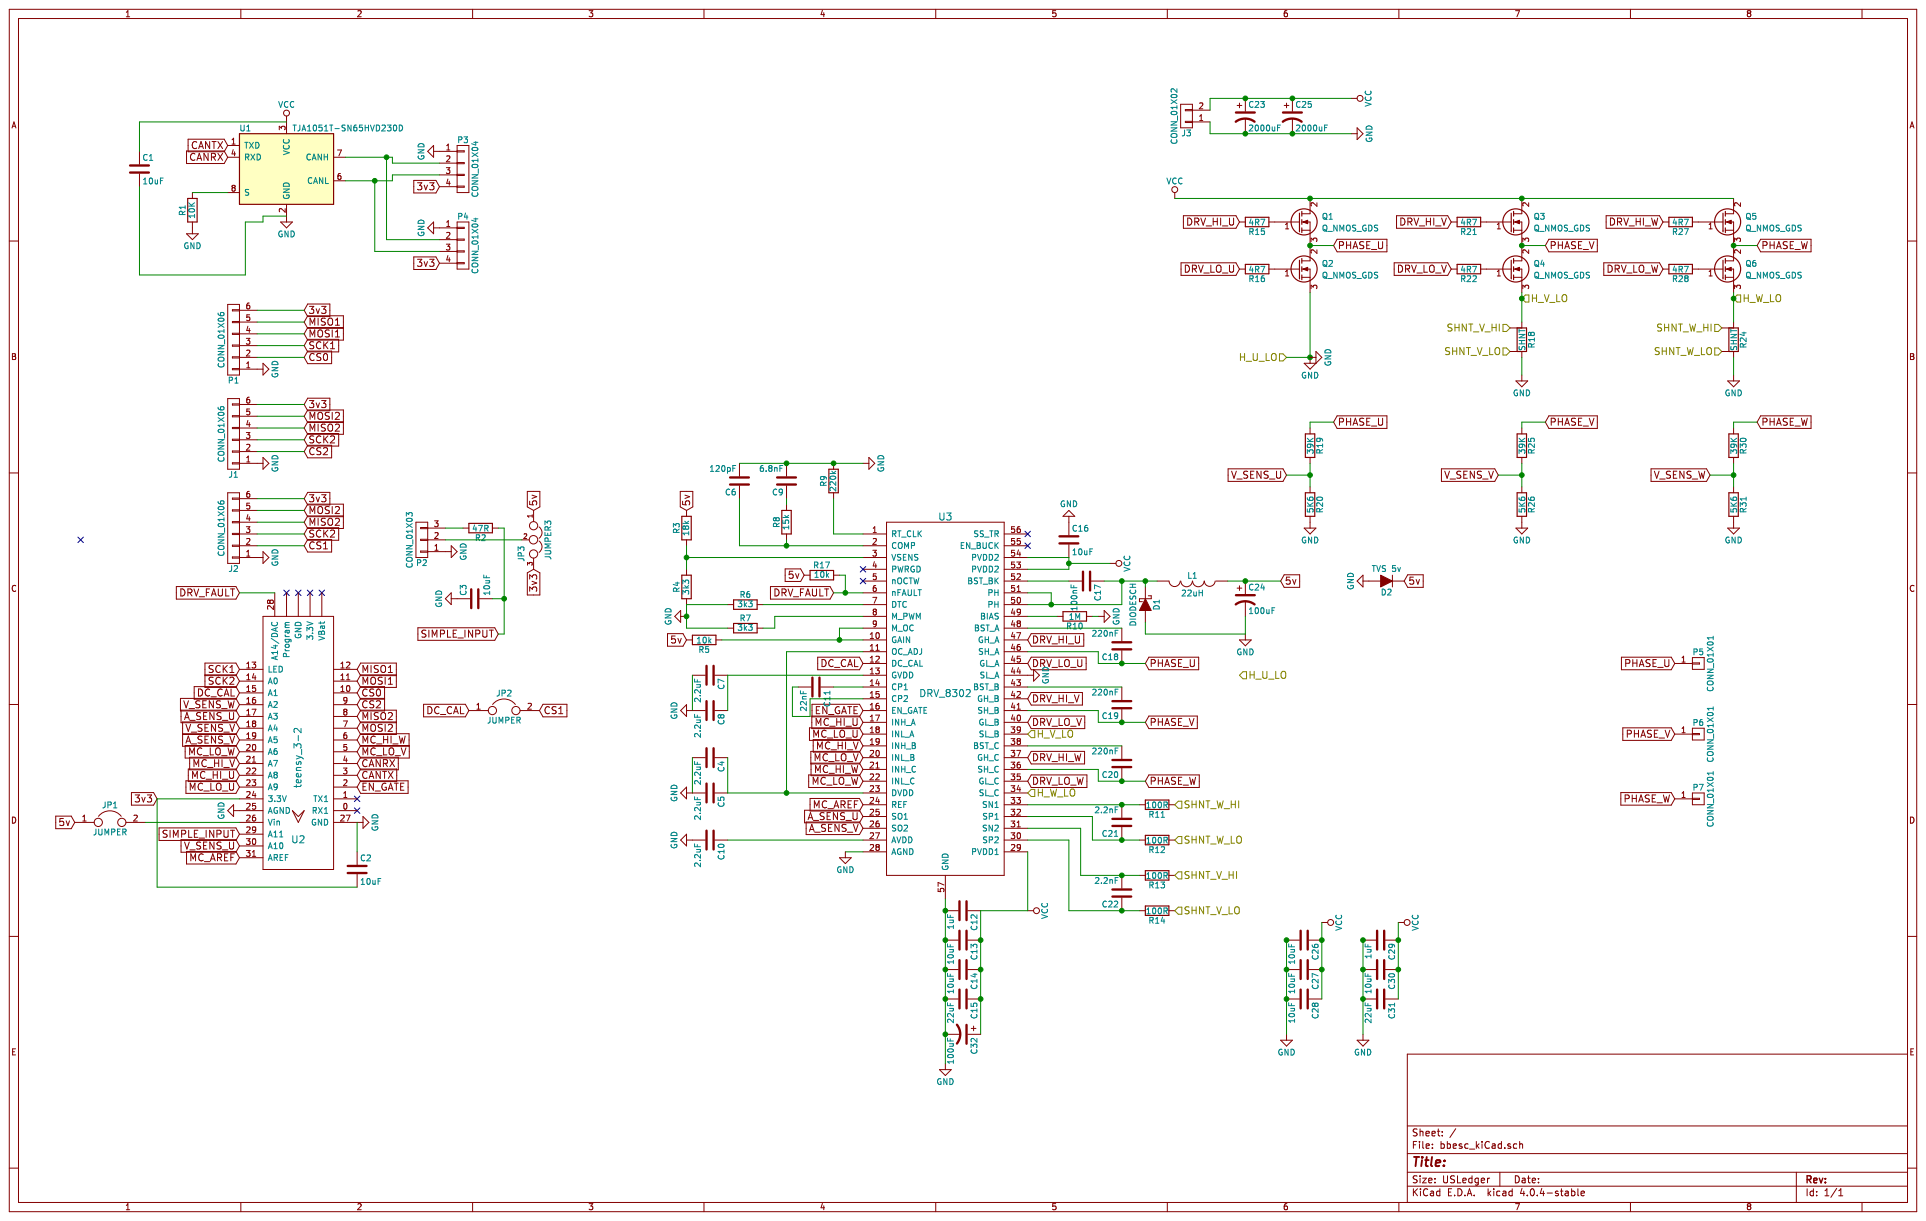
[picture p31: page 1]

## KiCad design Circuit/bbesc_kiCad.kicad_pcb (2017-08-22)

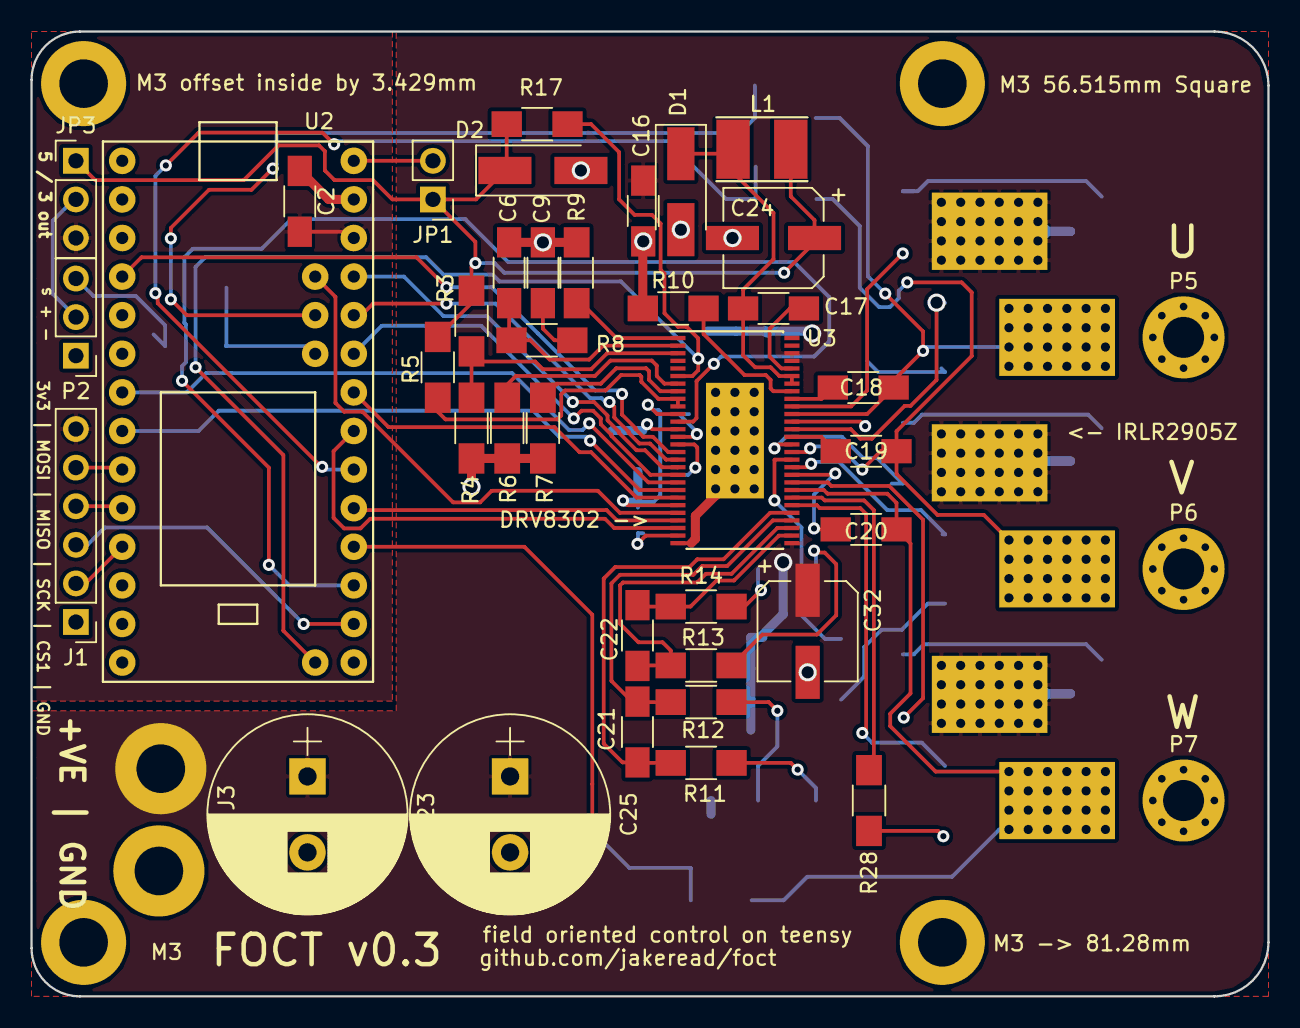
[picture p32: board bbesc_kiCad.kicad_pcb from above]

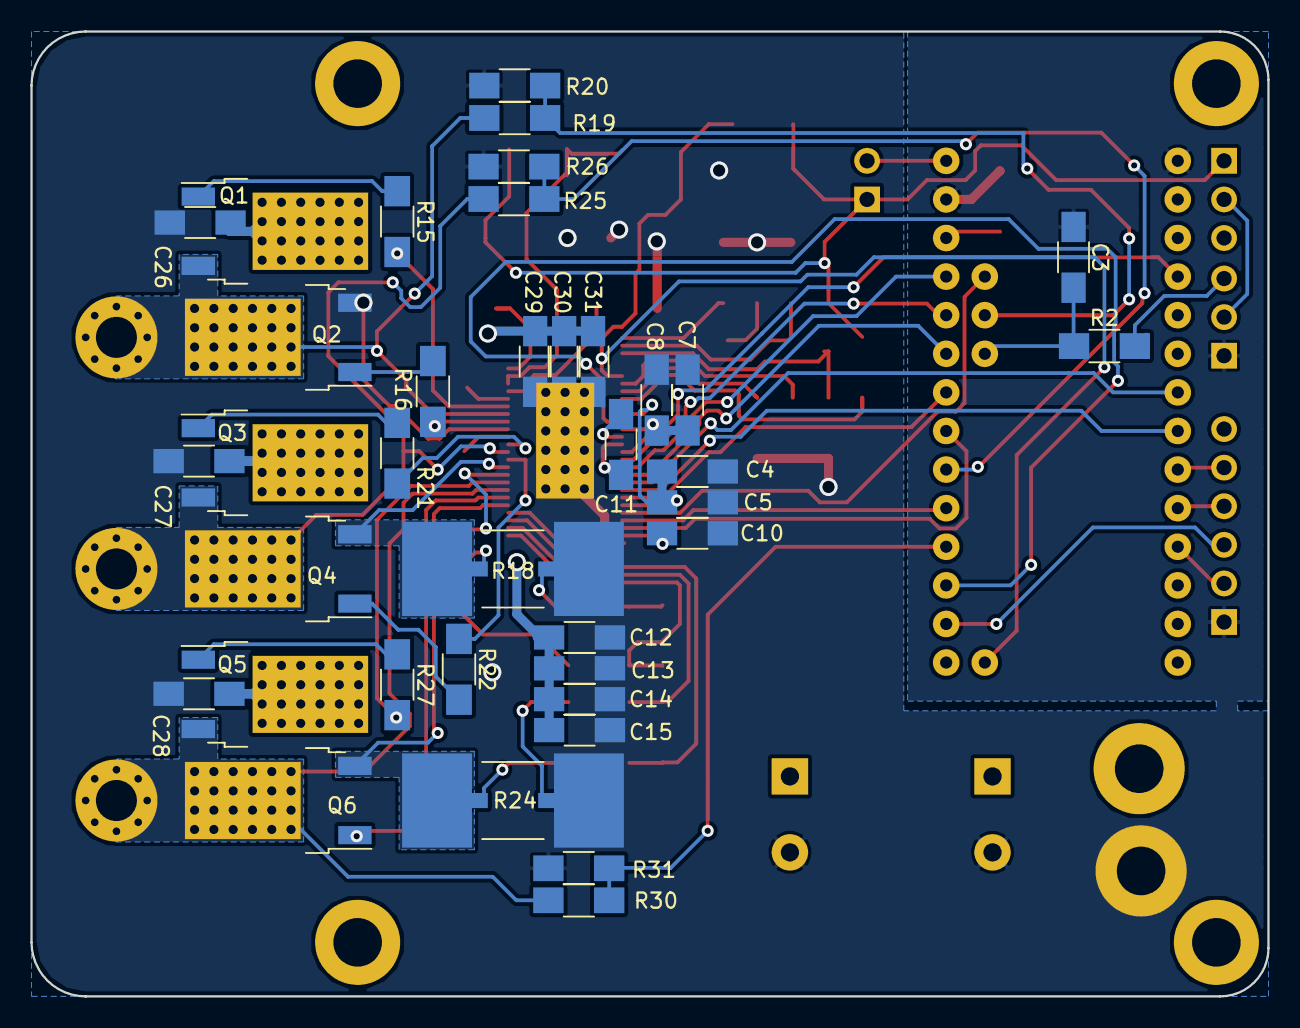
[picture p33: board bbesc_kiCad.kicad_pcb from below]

Board: 2 copper layers, 81.4 x 63.5 mm, 82 parts (37 on the bottom side), 70 nets.

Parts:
C2, C3, C13, C14, C16, C26, C27, C28, C29, C30, C31: 10uF; C_1206_HandSoldering
C4, C5, C7, C8, C10: 2.2uF; C_1206_HandSoldering
C6: 120pF; C_1206_HandSoldering
C9: 6.8nF; C_1206_HandSoldering
C11: 22nF; C_1206_HandSoldering
C12: 1uF; C_1206_HandSoldering
C15: 15uF; C_1206_HandSoldering
C17: 100nF; C_1206_HandSoldering
C18, C19, C20: 220nF; C_1206_HandSoldering
C21, C22: 2.2nF; C_1206_HandSoldering
C23, C25: 2000uF; CP_Radial_D13.0mm_P5.00mm
C24, C32: 100uF; CP_Elec_6.3x7.7
D1: DIODESCH; D_SMA_Handsoldering
D2: TVS 5v; D_SMA_Handsoldering
J1: CONN_01X06; Pin_Header_Straight_1x06_Pitch2.54mm
J3: CONN_01X02; WireConnection_2.50mmDrill_LargePad
JP1: JUMPER; Pin_Header_Straight_1x02_Pitch2.54mm
JP3: JUMPER3; Pin_Header_Straight_1x03_Pitch2.54mm
L1: 22uH; Inductor_Taiyo-Yuden_NR-40xx_HandSoldering
M3, M3 56.515mm Square, M3 -> 81.28mm, M3 offset inside by 3.429mm: MountingHole_3.2mm_M3_DIN965_Pad
P2: CONN_01X03; Pin_Header_Straight_1x03_Pitch2.54mm
P5, P6, P7: CONN_01X01; MountingHole_2.7mm_Pad_Via
Q1, Q2, Q3, Q4, Q5, Q6: Q_NMOS_GDS; TO-252-2
R2: 47R; R_1206_HandSoldering
R3: 18k; R_1206_HandSoldering
R4, R6, R7: 3k3; R_1206_HandSoldering
R5, R17: 10k; R_1206_HandSoldering
R8: 15k; R_1206_HandSoldering
R9: 220k; R_1206_HandSoldering
R10: 1M; R_1206_HandSoldering
R11, R12, R13, R14: 100R; R_1206_HandSoldering
R15, R16, R21, R22, R27, R28: 4R7; R_1206_HandSoldering
R18, R24: SHNT; R_SHUNT_3920
R19, R25, R30: 39K; R_1206_HandSoldering
R20, R26, R31: 5K6; R_1206_HandSoldering
U2: teensy_3-2; Teensy3.2-bottomLess
U3: DRV_8302; TSSOP-56_6.1x14mm_Pitch0.5mm

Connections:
3v3: C2.2, J1.6, JP3.3, U2.24
5v: C24.1, D2.1, JP1.1, JP3.1, L1.1, R3.2, R5.2, R17.1
/H_V_LO: Q4.3, R18.1, U3.39
/H_W_LO: Q6.3, R24.1, U3.34
/SHNT_V_HI: R13.1, R18.3
/SHNT_V_LO: R14.1, R18.4
/SHNT_W_HI: R11.1, R24.3
/SHNT_W_LO: R12.1, R24.4
A_SENS_U: U2.17, U3.25
A_SENS_V: U2.19, U3.26
CS2: J1.2, U2.9
DC_CAL: U2.15, U3.12
DRV_FAULT: R17.2, U2.28, U3.6
DRV_HI_U: R15.2, U3.47
DRV_HI_V: R21.2, U3.42
DRV_HI_W: R27.2, U3.37
DRV_LO_U: R16.2, U3.45
DRV_LO_V: R22.2, U3.40
DRV_LO_W: R28.2, U3.35
EN_GATE: U2.2, U3.16
GND: C2.1, C3.1, C4.2, C5.2, C6.2, C7.2, C8.2, C9.2, C10.2, C12.2, C13.2, C14.2, C15.2, C16.1, C23.2, C24.2, C25.2, C26.2, C27.2, C28.2, C29.2, C30.2, C31.2, C32.2, D1.2, D2.2, J1.1, J3.1, P2.1, Q2.3, R4.1, R6.1, R7.1, R9.2, R10.1, R18.2, R20.2, R24.2, R26.2, R31.2, U2.25, U2.27, U3.28, U3.44, U3.57
MC_AREF: U2.31, U3.24
MC_HI_U: U2.22, U3.17
MC_HI_V: U2.21, U3.19
MC_HI_W: U2.6, U3.21
MC_LO_U: U2.23, U3.18
MC_LO_V: U2.5, U3.20
MC_LO_W: U2.20, U3.22
MISO2: J1.4, U2.8
MOSI2: J1.5, U2.7
unnamed: C4.1, C5.1, U3.11, U3.23
unnamed: C6.1, R8.1, U3.2
unnamed: C7.1, C8.1, U3.13
unnamed: C9.1, R8.2
unnamed: C10.1, U3.27
unnamed: C11.1, U3.14
unnamed: C11.2, U3.15
unnamed: C17.1, D1.1, L1.2, U3.50, U3.51
unnamed: C17.2, U3.52
unnamed: C18.2, U3.48
unnamed: C19.2, U3.43
unnamed: C20.2, U3.38
unnamed: C21.1, R12.2, U3.32
unnamed: C21.2, R11.2, U3.33
unnamed: C22.1, R14.2, U3.30
unnamed: C22.2, R13.2, U3.31
unnamed: JP1.2, U2.26
unnamed: JP3.2, P2.2
unnamed: P2.3, R2.2
unnamed: Q1.1, R15.1
unnamed: Q2.1, R16.1
unnamed: Q3.1, R21.1
unnamed: Q4.1, R22.1
unnamed: Q5.1, R27.1
unnamed: Q6.1, R28.1
unnamed: R3.1, R4.2, U3.3
unnamed: R5.1, U3.9, U3.10
unnamed: R6.2, U3.7
unnamed: R7.2, U3.8
unnamed: R9.1, U3.1
unnamed: R10.2, U3.49
PHASE_U: C18.1, P5.1, Q1.3, Q2.2, R19.1, U3.46
PHASE_V: C19.1, P6.1, Q3.3, Q4.2, R25.1, U3.41
PHASE_W: C20.1, P7.1, Q5.3, Q6.2, R30.1, U3.36
SCK2: J1.3, U2.14
SIMPLE_INPUT: C3.2, R2.1, U2.29
VCC: C12.1, C13.1, C14.1, C15.1, C16.2, C23.1, C25.1, C26.1, C27.1, C28.1, C29.1, C30.1, C31.1, C32.1, J3.2, Q1.2, Q3.2, Q5.2, U3.29, U3.53, U3.54
V_SENS_U: R19.2, R20.1, U2.30
V_SENS_V: R25.2, R26.1, U2.18
V_SENS_W: R30.2, R31.1, U2.16

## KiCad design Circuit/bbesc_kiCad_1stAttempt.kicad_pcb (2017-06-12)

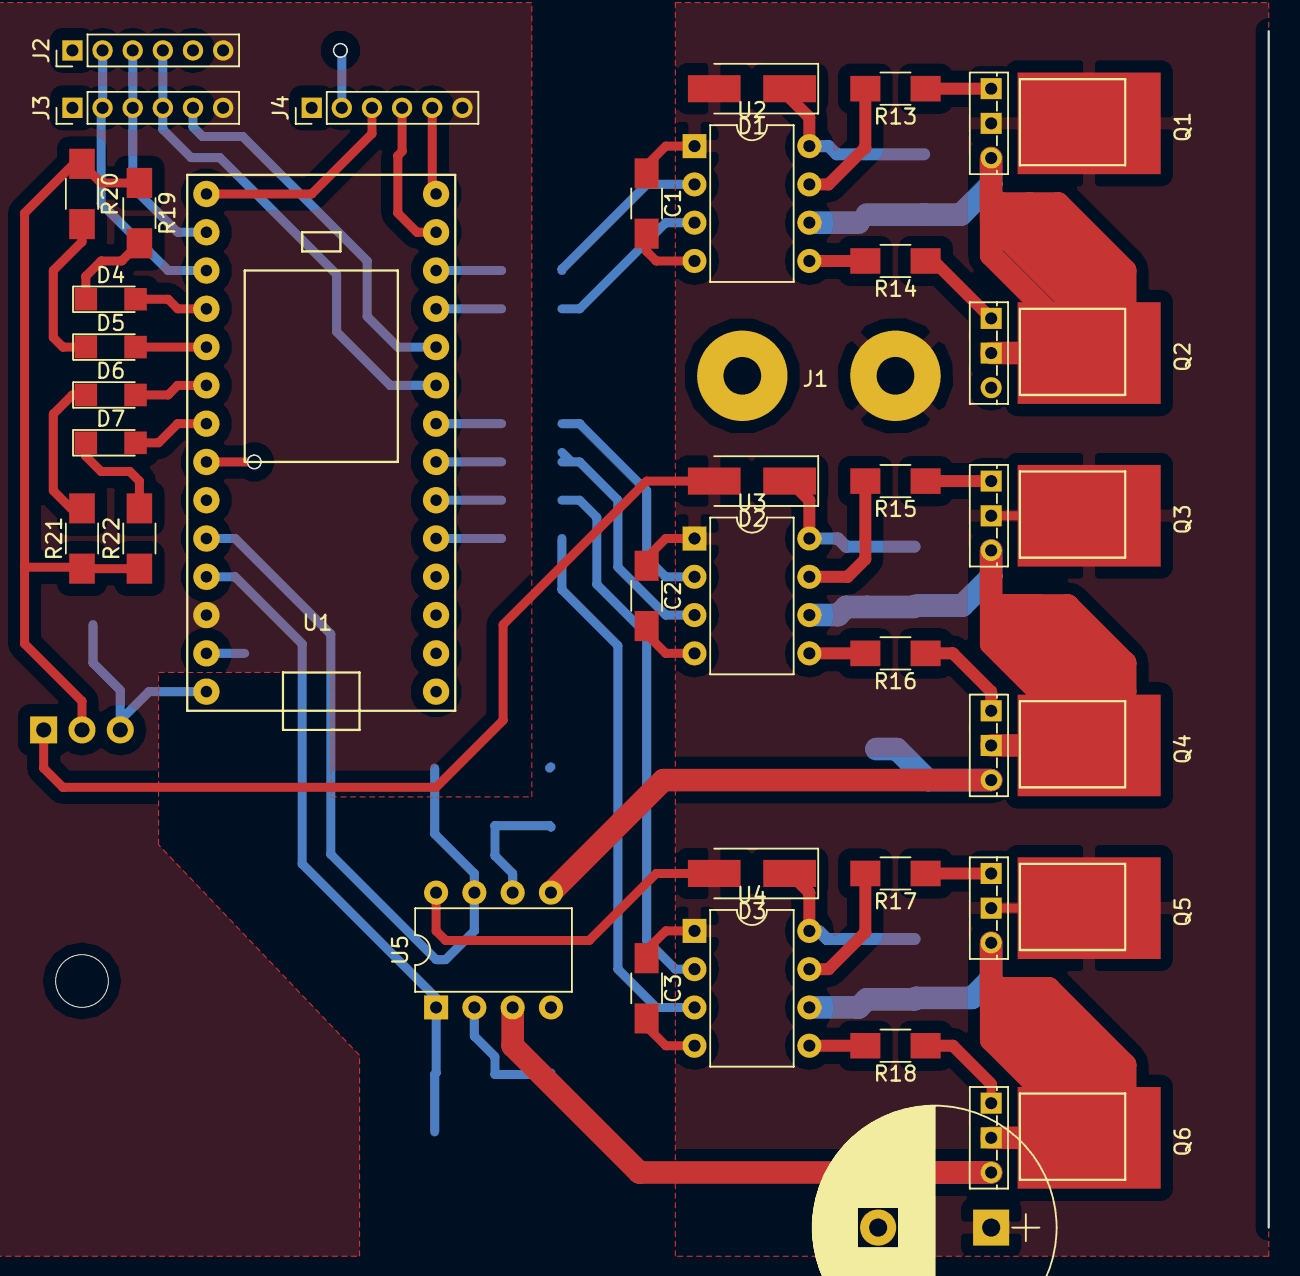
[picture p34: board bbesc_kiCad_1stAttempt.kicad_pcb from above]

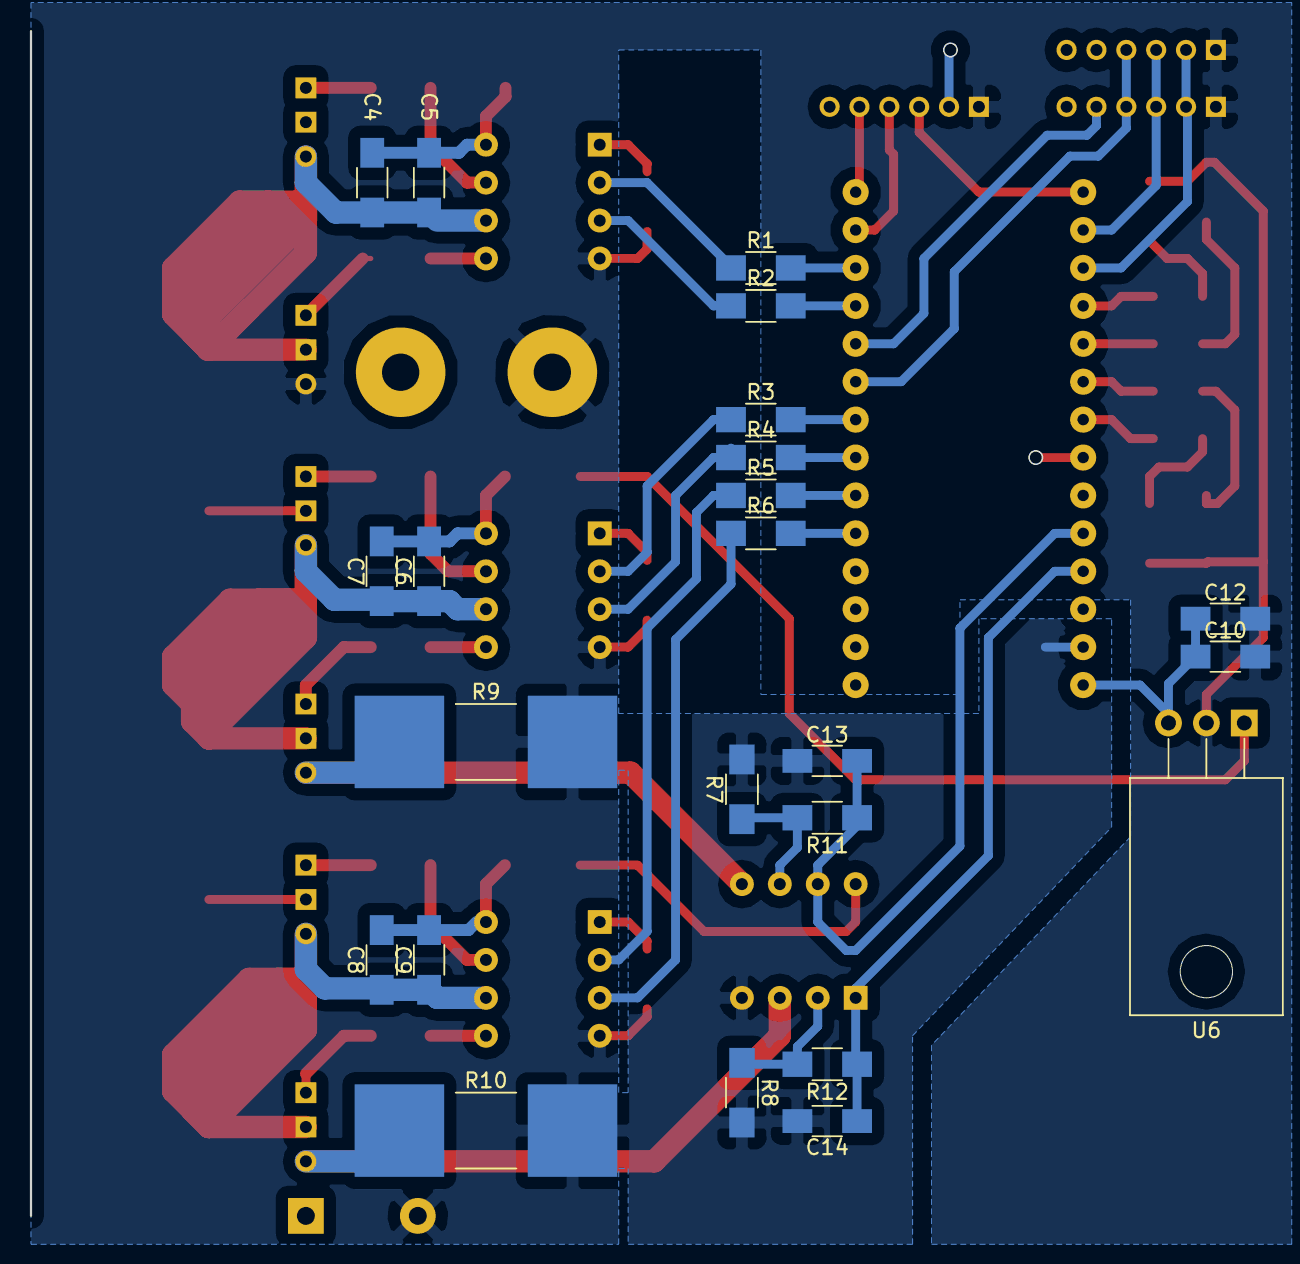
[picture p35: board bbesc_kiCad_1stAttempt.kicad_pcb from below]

Board: 2 copper layers, 59 parts (23 on the bottom side), 56 nets.

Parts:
C1, C2, C3, C10, C12: 1uF; C_1206_HandSoldering
C4, C6, C8: 10uF; C_1206_HandSoldering
C5, C7, C9, C13, C14: 0.1uF; C_1206_HandSoldering
C11: 2000uF; CP_Radial_D16.0mm_P7.50mm
D1, D2, D3: 1N4001; D_SMA_Handsoldering
D4, D5, D6, D7: LED; LED_1206
J1: CONN_01X02; WireConnection_2.50mmDrill_LargePad
J2, J3, J4: CONN_01X06; Pin_Header_Straight_1x06_Pitch2.00mm
Q1, Q2, Q3, Q4, Q5, Q6: Q_NMOS_GDS; TO-251_IPAK_Vertical
R1, R2, R3, R4, R5, R6: 470R; R_1206_HandSoldering
R7, R8: 12k; R_1206_HandSoldering
R9, R10: .001; R_2816_HandSoldering
R11, R12: 470k; R_1206_HandSoldering
R13, R14, R15, R16, R17, R18: 47R; R_1206_HandSoldering
R19, R20, R21, R22: 4K7; R_1206_HandSoldering
U1: teensy_3-2; Teensy3.2-bottomLess
U2, U3, U4: IR2101; DIP-8_W7.62mm
U5: LM358N; DIP-8_W7.62mm
U6: LM7805; TO-220_Horizontal

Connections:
3v3: J2.6, J3.6, J4.6, U1.24
CS1: J4.2, U1.20
CS2: J2.2, J3.2, U1.15
GND: C1.2, C2.2, C3.2, C10.2, C11.2, C12.2, C13.1, C14.2, J1.1, J2.1, J3.1, J4.1, Q2.3, R7.2, R8.2, R9.2, R10.2, R19.1, R20.1, R21.1, R22.1, U1.25, U1.27, U2.4, U3.4, U4.4, U5.4, U6.2
MISO1: J4.5, U1.12
MISO2: J3.5, U1.8
MOSI1: J4.4, U1.11
MOSI2: J2.4, J3.4, U1.7
unnamed: C4.1, C5.1, Q1.3, Q2.2, U2.6
unnamed: C4.2, C5.2, D1.1, U2.8
unnamed: C6.1, C7.1, Q3.3, Q4.2, U3.6
unnamed: C6.2, C7.2, D2.1, U3.8
unnamed: C8.1, C9.1, Q5.3, Q6.2, U4.6
unnamed: C8.2, C9.2, D3.1, U4.8
unnamed: C10.1, C12.1, U1.26, U6.3
unnamed: C13.2, R11.1, U1.22, U5.7
unnamed: C14.1, R12.1, U1.23, U5.1
unnamed: D4.1, R19.2
unnamed: D4.2, U1.16
unnamed: D5.1, R20.2
unnamed: D5.2, U1.17
unnamed: D6.1, R21.2
unnamed: D6.2, U1.18
unnamed: D7.1, R22.2
unnamed: D7.2, U1.19
unnamed: Q1.1, R13.1
unnamed: Q2.1, R14.1
unnamed: Q3.1, R15.1
unnamed: Q4.1, R16.1
unnamed: Q4.3, R9.1, U5.5
unnamed: Q5.1, R17.1
unnamed: Q6.1, R18.1
unnamed: Q6.3, R10.1, U5.3
unnamed: R1.1, U2.2
unnamed: R1.2, U1.10
unnamed: R2.1, U2.3
unnamed: R2.2, U1.9
unnamed: R3.1, U3.2
unnamed: R3.2, U1.6
unnamed: R4.1, U3.3
unnamed: R4.2, U1.5
unnamed: R5.1, U4.2
unnamed: R5.2, U1.4
unnamed: R6.1, U4.3
unnamed: R6.2, U1.3
unnamed: R7.1, R11.2, U5.6
unnamed: R8.1, R12.2, U5.2
unnamed: R13.2, U2.7
unnamed: R14.2, U2.5
unnamed: R15.2, U3.7
unnamed: R16.2, U3.5
unnamed: R17.2, U4.7
unnamed: R18.2, U4.5
SCK1: J4.3, U1.13
SCK2: J2.3, J3.3, U1.14
VCC: C1.1, C2.1, C3.1, C11.1, D1.2, D2.2, D3.2, J1.2, Q1.2, Q3.2, Q5.2, U2.1, U3.1, U4.1, U5.8, U6.1

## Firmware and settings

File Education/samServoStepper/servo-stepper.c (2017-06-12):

//
// servo stepper
//
// sec 2017
//
#include <stdio.h>
#include <avr/sleep.h>
#include <avr/interrupt.h>
#include "serial.h"
//#include "spi.h"
//calibration offsets for ADC
#define ADCACAL0_offset 0x20
#define ADCACAL1_offset 0x21
#define DEAD_TIME_CYCLES 2 //Dead time length, given in main system clock cycles.
#define ADC_SAMPLES 10 //adc samples to average for current measurement

static char input_buffer[100] = {0};
char checksum = 0;
USART_data_t USART_data;
int position_in_buffer = 0;
uint16_t angle = 0;

//currents through phases
uint16_t cur_1[ADC_SAMPLES];
uint16_t cur_2[ADC_SAMPLES];
uint16_t cur_1_avg = 0;
uint16_t cur_2_avg = 0;
uint16_t cur_pointer = 0;

//functions to set pwm and direction on motors
void set_pwms(uint16_t cca, uint16_t ccb, uint16_t ccc, uint16_t ccd){
	TCC0.CCABUF = cca;
	TCC0.CCBBUF = ccb;
	TCC0.CCCBUF = ccc;
	TCC0.CCDBUF = ccd;
	do {} while(TCC0.INTFLAGS && TC0_OVFIF_bm == 0 );  //wait
	TCC0.INTFLAGS = TC0_OVFIF_bm;
}


void send_packet(){
	usart_send_byte(&USART_data,200);
	usart_send_byte(&USART_data,200);
	usart_send_byte(&USART_data,200);
	usart_send_byte(&USART_data,200);
	usart_send_byte(&USART_data,200);
	usart_send_uint16(&USART_data,TCC0.CCABUF);
	usart_send_uint16(&USART_data,TCC0.CCBBUF);
	usart_send_uint16(&USART_data,TCC0.CCCBUF);
	usart_send_uint16(&USART_data,TCC0.CCDBUF);
	usart_send_uint16(&USART_data,angle);
	usart_send_uint16(&USART_data,cur_1_avg);
	usart_send_uint16(&USART_data,cur_2_avg);
	usart_send_byte(&USART_data,201);
	usart_send_byte(&USART_data,201);
	usart_send_byte(&USART_data,201);
	usart_send_byte(&USART_data,201);
	usart_send_byte(&USART_data,201);
}
void send_ack(){
	usart_send_byte(&USART_data,200);
	usart_send_byte(&USART_data,200);
	usart_send_byte(&USART_data,200);
	usart_send_byte(&USART_data,200);
	usart_send_byte(&USART_data,200);
	usart_send_byte(&USART_data,6);
	usart_send_byte(&USART_data,201);
	usart_send_byte(&USART_data,201);
	usart_send_byte(&USART_data,201);
	usart_send_byte(&USART_data,201);
	usart_send_byte(&USART_data,201);	
}

void spi_transcieve_uint16(uint16_t data, uint16_t *result){
	//send 16 bit command frame data, recieve 16 data frame, assign to variable with pointer result
	PORTD.OUTCLR = PIN4_bm; //Pull SS line low
	SPID.DATA = (data >> 8); //upper byte first
	while(!(SPID.STATUS & SPI_IF_bm)) {}
	*result = ((uint16_t)SPID.DATA << 8);
	SPID.DATA = (data & 0xFF); //lower byte next
	while(!(SPID.STATUS & SPI_IF_bm)) {}
	*result |= SPID.DATA;
	PORTD.OUTSET = PIN4_bm; //Pull SS line high
}

void parse_packet(char* buffer){
	checksum = 0;
	for( int i=5; i<position_in_buffer-5; ++i) {checksum += buffer[i];}
	if (checksum == buffer[position_in_buffer-5] && buffer[0]==(char)200 && buffer[1]==(char)200 && buffer[2]==(char)200 && buffer[3]==(char)200 && buffer[4]==(char)200){
		send_ack();
		char id = buffer[5];
		if (id==110){
			//_delay_us(100);
			//can we do this only if we've accumulated an appropriate number of samples?
			send_packet();
		} else if (id==100){
			//set pwms directly
			set_pwms(
				parse_uint16(&buffer[6]),
				parse_uint16(&buffer[8]),
				parse_uint16(&buffer[10]),
				parse_uint16(&buffer[12])
				);
		} else if (id==101){
			//read register on as5047d
			//first bit is parity, calculated on lower 15 bits of frame
			//second bit is command type, 0 for write, 1 for read
			//other bits are address
			//spi_transcieve_uint16(( 1<<15 ) | ( 1<<14 ) | ( 0x3FFF ), &angle); //address, ANGLECOM
			spi_transcieve_uint16(( 0<<15 ) | ( 1<<14 ) | ( 0x3FFD ), &angle); //address, MAG, lower 13 bits
			//spi_transcieve_uint16(( 1<<15 ) | ( 1<<14 ) | ( 0x3FFC ), &angle); //address, DIAAGC
			//spi_transcieve_uint16(( 0 << 15 ) | ( 1 << 14 ) | 0x0001, &angle ); //address, ERRFL
			
			_delay_us(1); //must be greater than 350 ns between frames
			spi_transcieve_uint16(0x0000, //no op
							&angle); //read result
			angle &= 0x1FFF; //for mag, just keep lower 13 bits

		}

	}
}

void read_usart(){
	if (USART_RXBufferData_Available(&USART_data)) {
		input_buffer[position_in_buffer] = USART_RXBuffer_GetByte(&USART_data);
		if (input_buffer[position_in_buffer] == (char)201 && 
			input_buffer[position_in_buffer-1] == (char)201 &&
			input_buffer[position_in_buffer-2] == (char)201 &&
			input_buffer[position_in_buffer-3] == (char)201 &&
			input_buffer[position_in_buffer-4] == (char)201 &&
			((position_in_buffer == 19) || (position_in_buffer == 11)) //check against expected lengths
			){
			parse_packet(input_buffer);
			position_in_buffer = 0;
		}
		else{
			position_in_buffer++;
		}
	}
}

//TODO: set up ADC for current measurement
//TODO: set up DMA to transfer encoder value to variable.

int main(void) {
	// set up clock
	OSC.CTRL = OSC_RC32MEN_bm; // enable 32MHz clock
	while (!(OSC.STATUS & OSC_RC32MRDY_bm)); // wait for clock to be ready
	CCP = CCP_IOREG_gc; // enable protected register change
	CLK.CTRL = CLK_SCLKSEL_RC32M_gc; // switch to 32MHz clock

	//set up usart
	PORTE.DIRSET = PIN3_bm; //TXE0
	PORTE.DIRCLR = PIN2_bm; //RXD0
	USART_InterruptDriver_Initialize(&USART_data, &USARTE0, USART_DREINTLVL_LO_gc);
	USART_Format_Set(USART_data.usart, USART_CHSIZE_8BIT_gc,
                     USART_PMODE_DISABLED_gc, 0);
	//USARTE0.CTRLC = (USARTE0.CTRLC & ~USART_CMODE_gm) | USART_CMODE_ASYNCHRONOUS_gc;

	USART_RxdInterruptLevel_Set(USART_data.usart, USART_RXCINTLVL_LO_gc);
	//take f_sysclk/(BSEL+1) ~= f_baud*16 with zero scale.  See manual or spreadsheet for scale defs
	USART_Baudrate_Set(&USARTE0, 123 , -4); //230400 baud with .08% error
	USART_Rx_Enable(USART_data.usart);
	USART_Tx_Enable(USART_data.usart);

	//
	//TCC0 AWEX and DTI for driving hbridge
	//
	AWEXC.CTRL |= AWEX_DTICCAEN_bm | AWEX_DTICCBEN_bm | AWEX_DTICCCEN_bm | AWEX_DTICCDEN_bm;
	AWEXC.OUTOVEN = 0xFF; //override all pins on port c for awex
	AWEXC.DTLS = DEAD_TIME_CYCLES;
	AWEXC.DTHS = DEAD_TIME_CYCLES;
	PORTC.DIR = 0xFF; //Enable output on PORTC.
	TCC0.PER = 0x0FFF;
	TCC0.CTRLB = TC0_CCAEN_bm | TC0_CCBEN_bm | TC0_CCCEN_bm | TC0_CCDEN_bm | TC_WGMODE_SS_gc;
	//TCC0.INTCTRLA = TC_OVFINTLVL_LO_gc; //overflow interrupt
	TCC0.CTRLA = ( TCC0.CTRLA & ~TC0_CLKSEL_gm ) | TC_CLKSEL_DIV1_gc; //start TCC0


	//SPI
	PORTD.REMAP |= PORT_SPI_bm; //swap SCK to PD5 and MOSI to PD7
	PORTD.DIRSET = PIN4_bm;		//Init SS pin as output
	PORTD.PIN4CTRL = PORT_OPC_WIREDANDPULL_gc; 	// with wired AND and pull-up.
	PORTD.OUTSET = PIN4_bm;  // Set SS output to high. (No slave addressed).
	SPID.CTRL = SPI_PRESCALER_DIV4_gc | //SPI prescalar (32 MHz / 4 = 8 MHz)
				SPI_CLK2X_bm | 			//double clock speed (32 MHz / 4 = 8 MHz x 2 = 16 MHz)
				SPI_ENABLE_bm | 		//enable spi module
				SPI_MASTER_bm | 		//SPI Master mode
				SPI_MODE_1_gc; 			//SPI mode, see app note 1309 and AS5047D datasheet
	PORTD.DIRSET = PIN5_bm | PIN7_bm; //set CLK and MOSI to outputs

	//ADC for current measurement
	//calibrate to reduce nonlinearity
	NVM_CMD = NVM_CMD_READ_CALIB_ROW_gc;
	ADCA.CALL = pgm_read_byte(PROD_SIGNATURES_START + ADCACAL0_offset);
	NVM_CMD = NVM_CMD_READ_CALIB_ROW_gc;
	ADCA.CALL = pgm_read_byte(PROD_SIGNATURES_START + ADCACAL1_offset);
	NVM_CMD = NVM_CMD_NO_OPERATION_gc;

	ADCA.CTRLB = (ADCA.CTRLB & ~ADC_RESOLUTION_gm) |  ADC_RESOLUTION_8BIT_gc; //set resolution
	ADCA.REFCTRL = (ADCA.REFCTRL & ~ADC_REFSEL_gm) | ADC_REFSEL_INT1V_gc; //set reference
	ADCA.PRESCALER = (ADCA.PRESCALER & ~ADC_PRESCALER_gm) | ADC_PRESCALER_DIV64_gc; //set prescalar
	
	//ADCA, channel zero, cur_1
	ADCA.CH0.CTRL = (ADCA.CH0.CTRL & ~ADC_CH_INPUTMODE_gm) | ADC_CH_INPUTMODE_DIFFWGAIN_gc; //set differential with gain
	ADCA.CH0.CTRL = (ADCA.CH0.CTRL & ~ADC_CH_GAIN_gm) | ADC_CH_GAIN_4X_gc; //set gain
	ADCA.CH0.MUXCTRL = (uint8_t) ADC_CH_MUXPOS_PIN6_gc | ADC_CH_MUXNEG_GND_MODE4_gc;
	ADCA.CH0.INTCTRL = ADC_CH_INTMODE_COMPLETE_gc | ADC_CH_INTLVL_HI_gc;
	
	//ADCA, channel one, cur_2
	ADCA.CH1.CTRL = (ADCA.CH1.CTRL & ~ADC_CH_INPUTMODE_gm) | ADC_CH_INPUTMODE_DIFFWGAIN_gc; //set differential with gain
	ADCA.CH1.CTRL = (ADCA.CH1.CTRL & ~ADC_CH_GAIN_gm) | ADC_CH_GAIN_4X_gc; //set gain
	ADCA.CH1.MUXCTRL = (uint8_t) ADC_CH_MUXPOS_PIN7_gc | ADC_CH_MUXNEG_GND_MODE4_gc;
	ADCA.CH1.INTCTRL = ADC_CH_INTMODE_COMPLETE_gc | ADC_CH_INTLVL_HI_gc;	
	
	ADCA.EVCTRL = (ADCA.EVCTRL & ~ADC_SWEEP_gm) | ADC_SWEEP_01_gc; //set sweep over channels 0,1
	ADCA.EVCTRL = (ADCA.EVCTRL & ~ADC_EVSEL_gm) | ADC_EVSEL_67_gc; //event channels 6,7 as inputs
	ADCA.EVCTRL = (ADCA.EVCTRL & ~ADC_EVACT_gm) | ADC_EVACT_SWEEP_gc; //event channel 6 triggers adc sweep
	ADCA.CTRLA |= ADC_ENABLE_bm; //enable ADCA

	ADCA.CH1.INTCTRL = ADC_CH_INTMODE_COMPLETE_gc | ADC_CH_INTLVL_LO_gc; //set up interrupts on ADC CH1
	ADCA.INTFLAGS = ADC_CH1IF_bm; //clear interrupt flag

	//use TCC0 overflow to start adc sweep
	EVSYS.CH6MUX = EVSYS_CHMUX_TCC0_OVF_gc;


	//DAC for resistor network reference
	DACB.CTRLB = ( DACB.CTRLB & ~DAC_CHSEL_gm ) | DAC_CHSEL_DUAL_gc;
	DACB.CTRLC = ( DACB.CTRLC & ~( DAC_REFSEL_gm ) ) | DAC_REFSEL_INT1V_gc;
    DACB.CTRLA |= DAC_CH1EN_bm | DAC_CH0EN_bm | DAC_ENABLE_bm;
	DACB.CH0DATA = 4095; //set to 1V
	DACB.CH1DATA = 4095; //set to 1V


	PMIC.CTRL |= PMIC_LOLVLEX_bm;//enable low level interrupts
	sei();

	while (1) {
		read_usart();
	}
	return 0;
}

ISR(USARTE0_RXC_vect){USART_RXComplete(&USART_data);}
ISR(USARTE0_DRE_vect){USART_DataRegEmpty(&USART_data);}

ISR(ADCA_CH1_vect){
	//cur_1_avg -= cur_1[cur_pointer]; //subtract old value
	//cur_2_avg -= cur_2[cur_pointer];
	//cur_1[cur_pointer] = ADCA.CH0.RESL; //replace old value
	//cur_2[cur_pointer] = ADCA.CH1.RESL; 
	//cur_1_avg += cur_1[cur_pointer]; //add back new value
	//cur_2_avg += cur_2[cur_pointer];
	cur_1_avg = ADCA.CH0.RESL & ~(1<<7); //get rid of sign bit
	cur_2_avg = ADCA.CH1.RESL & ~(1<<7); //get rid of sign bit
	if( cur_pointer < ADC_SAMPLES-1){EVSYS.STROBE = 1<<6;} //trigger event channel 6 to start another sweep
	cur_pointer = (cur_pointer+1)%ADC_SAMPLES;
}

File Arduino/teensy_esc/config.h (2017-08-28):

#ifndef CONFIG_H
#define CONFIG_H

#define TRUE                        1
#define FALSE                       0

// STARTUP

#define GO_ON_STARTUP               TRUE

// COM

#define THE_BAUDRATE                115200

// PINS

// BLDC Specific (uses abstracted pwm) (SVPWM / FOC PWM modules use register-written pin configs in t3pwm.cpp)
#define PIN_HI_U                    22
#define PIN_LO_U                    23
#define PIN_HI_V                    21
#define PIN_LO_V                    5
#define PIN_HI_W                    6
#define PIN_LO_W                    20

// ADC for Voltages (adc for amperage measurement is linked to t3adc.cpp register-writing)
#define PIN_VSENS_U                 A2
#define PIN_VSENS_V                 A4
#define PIN_VSENS_W                 A10

// ENCODER SETUPS

#define AS5047_SAMPLE_RATE          20000

#define AS5047_RESOLUTION           16384 
#define AS5047_SAMPLES              256             // keep lots of these around so that we can do filtering, derivatives
#define AS5047_AVERAGING            4

#define RBUF_LENGTH                 256

#define AS5047_OFFSET_BLDC          364           // but ~ 1700 seems better -> this is roughly one 'com zone' away
#define AS5047_OFFSET_FOC           999
#define AS5047_REV_BLDC             TRUE          // set TRUE to reverse values, 0 to retain original // MT4108 = TRUE // MT5208 = FALSE
#define AS5047_REV_FOC              TRUE

#define ENCODER_REVSEARCH_NUM       5
#define ENCODER_REVSEARCH_MULTIPLE  25 // _NUM * 6 ... TODO: evaluations in #defines?
#define ENCODER_REVSEARCH_LESS      24
#define ENCODER_SEARCH_DEFAULT_DUTY 1024

// MOTOR SPECIFIC

#define MOTOR_POLEPAIRS             11    // MT5208 = 7 // MT4108 = 11
#define MOTOR_MODULO                1489  // AS5047_RESOLUTION / MOTOR_POLEPAIRS // // MT4108 = 1489 || MT5208 = 2340 = resolution / poles / 2

// DRIVER

#define LEG_PWMRES                  8
#define LEG_PWMFREQ                 187500
#define LEG_MINPWM                  64


// LOOP SPEEDS

#define MACHINE_LOOP_DEFAULT_HZ     8000
#define MACHINE_LOOP_SECONDARY      10000
#define SAMPLE_DEFAULT_HZ           10000

// SVM

#define PHASE_ADVANCE               1.45 // RADIANS: optimum is 90*, or PI/2, or 1.57
#define POS_TO_THETA                0.0042197349

// FOC

#define V_REF                       1.65f // half of VREF from Teensy, see DRV8302 datasheet, REF pin
#define V_BUS                       12.0f
#define CURRENT_SHUNT_RES           0.002
#define CURRENT_AMP_GAIN            40
#define CURRENT_AMP_OFFSET_V        2048 // observed amp output at 0 current, in raw adc num
#define CURRENT_AMP_OFFSET_W        2048

// BLDC

#define IS_BLDC_MACHINE             0
#define IS_FOC_MACHINE              1

#define BLDC_MAX_OL_FREQ            10000

#define BLDC_INPUTMODE_POT          1
#define BLDC_INPUTMODE_SHELL        0

#define BLDC_DEFAULT_DUTY           1500 // of 4096
#define BLDC_DEFAULT_DIR            1
#define BLDC_DEFAULT_HZ             124

#if IS_BLDC_MACHINE && IS_FOC_MACHINE
#warning WTF
#endif

// DEBUG POT

#define DEBUG_POT_PIN               A14

// SP

#define ARGWORDS                    4

#endif

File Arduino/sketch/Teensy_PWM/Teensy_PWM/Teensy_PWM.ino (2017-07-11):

/*
BLDC Test Programm
Only Signal generation
Sinwave 6Phase Signal
PWM-Brake

signals pins:
pin 22 channel 00 phase U-high
pin 23 channel 01 phase U-low
pin 09 channel 02 phase V-high
pin 10 channel 03 phase V-low
pin 06 channel 04 phase W-high
pin 20 channel 05 phase W-low

pin 13 Trigger out01 if high PWM is switch off
pin 14 Trigger out02 if high PWM break starts

11.07.2014 Barney
*/

#include "pwm.h"

#define PERIPHERAL_BUS_CLOCK 48000000   // Bus Clock 48MHz
#define FTM0_CLK_PRESCALE 0             // FTM0 Prescaler
#define FTM0_OVERFLOW_FREQUENCY 80000   // PWM frequency in Hz
#define FTM0_DEADTIME_DTVAL 5           // DeadTimeHigh, zum Schutz der MOSFETs

// Berechnen von max und min Tastverhaeltnis 
const uint16_t MAX_DUTY_CYCLE = PERIPHERAL_BUS_CLOCK/FTM0_OVERFLOW_FREQUENCY;     // Maximum duty cycle value.
const uint16_t MIN_DUTY_CYCLE = 0;      // Minimum duty cycle value.

// Sinustabelle normiert auf Amplitudenwert 300, positive Halbwelle und 180 Grad Nullwerte, 2 Grad Winkelaufloesung 
const uint16_t sintable[]={
  0,10,21,31,42,52,62,73,83,93,103,112,122,132,141,150,159,168,176,185,193,201,208,216,223,230,236,243,249,254,
  260,265,270,274,278,282,285,288,291,293,295,297,298,299,300,300,300,299,298,297,295,293,291,288,285,282,278,274,
  270,265,260,254,249,243,236,230,223,216,208,201,193,185,176,168,159,150,141,132,122,112,103,93,83,73,62,52,42,31,
  21,10,0,0,0,0,0,0,0,0,0,0,0,0,0,0,0,0,0,0,0,0,0,0,0,0,0,0,0,0,0,0,0,0,0,0,0,0,0,0,0,0,0,0,0,0,0,0,0,0,0,0,0,0,0,
  0,0,0,0,0,0,0,0,0,0,0,0,0,0,0,0,0,0,0,0,0,0,0,0,0,0,0,0,0,0,0,0,0,0,0,0,0,0};

// Phasenlage von u,v,w
byte u = 0;       // Phase U ->   0 degree reference
byte v = 180-60;  // Phase V -> 120 degrees later
byte w = 180-120; // Phase W -> 240 degrees later

uint16_t BreakPower = 0;
byte Ramp = 1;    // Spannungsabsenkung bei kleinen Drehzahlen

int test = 0;     // for some tests
int Trigger_01 = 13;
int Trigger_02 = 14;


void setup () {
  // initialize the digital pin as an output.
  pinMode(Trigger_01, OUTPUT);    
  digitalWrite(Trigger_01, LOW);

  pinMode(Trigger_02, OUTPUT);    
  digitalWrite(Trigger_02, LOW);
  PWMInit(PERIPHERAL_BUS_CLOCK, FTM0_CLK_PRESCALE, FTM0_OVERFLOW_FREQUENCY, FTM0_DEADTIME_DTVAL);
}

void loop (){
  // Diverse Tests
  test ++;

  if (test < 1400 || test > 1850 & test < 2200) {
    //delayMicroseconds(1); 
    PWM_SetDutyCycle(sintable[u]/Ramp,sintable[v]/Ramp,sintable[w]/Ramp);  // PWM-Tastverhaeltnis fuer Phase u setzen, Aplitude skalieren
  }


  if (test == 1400) {
    digitalWrite(Trigger_02, HIGH);     // Trigger fuer LA
    // PWM Bremse
    // Fuer die PWM-Bremse muessen die oberen MOSFETS abgeschaltet werden
    // Achtung Registerdokumentaion in pwmc.c ist falsch. Das Datenblatt des Microkontrollers ist zu nehmen
    BreakPower = 0;                 // PWM switch off
    PWM_BreakeMode();
    PWM_Break(BreakPower);          // PWM-Tastverhaeltnis fuer Phase u setzen
  }

  if (test > 1450 && test < 1700) {
      // Bremsen
      BreakPower++;
      PWM_Break(BreakPower);        // PWM-Tastverhaeltnis fuer Phase u setzen
    }

  if (test == 1850) {

    BreakPower = 0;                 // Bremse loesen und alle Ausgaenge auf Normalbetrieb
    PWM_Break(BreakPower);          // PWM-Tastverhaeltnis fuer Phase u setzen
    PWM_BreakeModeEnd();            // Ende PWM Bremse
  }

  if (test == 2200) {
    digitalWrite(Trigger_01, HIGH); // Trigger for logic analyser
    PWM_Force0();                   // PWM switch off
   }

 
  u++;
  if (u == 180) u=0;
  v++;
  if (v == 180) v=0;
  w++;
  if (w == 180) w=0;
}

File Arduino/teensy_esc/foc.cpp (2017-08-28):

#include "foc.h"
#include "kernel.h"
#include "as5047.h"
#include "t3pwm.h"

#include "fastrig.h"
using namespace FASTRIG;

volatile long FOC::_loopCount = 0;
volatile float FOC::_p = 0;

FOC::FOC() {
  t3pwm = new T3PWM();
  t3adc = new T3ADC();

  analogWriteResolution(12);

  _id_err_int_rb = new RingBufferFloat();
  _iq_err_int_rb = new RingBufferFloat();
}

void FOC::init() {
  t3pwm->init(); // TODO: just T3PWM, pls
  t3adc->init();

  ftTableInit();

  _id_err_int_rb->clear();
  _iq_err_int_rb->clear();

  _i_scalar = ( V_REF / 2048 ) / ( CURRENT_SHUNT_RES * CURRENT_AMP_GAIN );

  _loopCount = 0;
  KERNEL->gateEnableOn();
}

//float mapfloat(float val, float fromLo, float fromHi, float toLo, float toHi){
//return ((val - fromLo) / (fromHi - fromLo)) * (toHi - toLo);
//}

#define KP_D          6.0f    // volts / amp(error)
#define KP_Q          6.0f
#define KI_D          0.1f
#define KI_Q          0.1f
#define K_LIMIT_INT   V_BUS/4
#define K_LIMIT_TOTAL V_BUS/2 // carefully


void FOC::onMainLoop() {
  KERNEL->flashLed();
  _loopCount ++;

  /*
   * CURRENT MEASUREMENT
     all sampling runs 'in the background' on ADC / FTM0 interrupts
     so at first we load the values from their ringbuffers into the variables we'll use for the duration of the loop
  */
  float _iv = (t3adc->rbav->latest() - CURRENT_AMP_OFFSET_V) * _i_scalar; // 1-2-3, 10us
  float _iw = (t3adc->rbaw->latest() - CURRENT_AMP_OFFSET_W) * _i_scalar;
  float _iu = -_iv - _iw;

  /*
   * POSITION MEASUREMENT
   * we sample this 'directly' by talking to the encoder class. this triggers SPI footwork to read from the encoder.
   * inside the encoder class we do some pretty low-tech filtering, and we use a filtered output rather than the direct reading (which is noisy!)
   * TODO: in other versions, the encoder sampled in the background on a timer at ~30kHz, and then samples were loaded out of a ringbuffer a-la the 
   * current sensing above. I think this might be a better solution, and it allows for better filtering.
   * Good position data seems critical.
   */
  KERNEL->as5047->readNow();
  float _elecpos = KERNEL->as5047->filteredInt() % MOTOR_MODULO;
  float _theta = (float)_elecpos / MOTOR_MODULO * TWO_PI; // this float conversion takes ~10us :/

  /*
     the Clarke transform takes these u, v, w current values and transforms them into the static AB frame
  */
  float _ia = TWO_OVER_THREE * ( _iu - 0.5f * _iv - 0.5f * _iw );
  float _ib = TWO_OVER_THREE * ( SQRT_THREE_OVER_TWO * _iv - SQRT_THREE_OVER_TWO * _iw );

  /*
     now we do a Parke transform, which results in a current measurement in the DQ frame that rotates along with the rotor. 
     note on electric vs. mechanical rotor-position:
     _theta is the 'electric' position of the rotor, as in how far long one phase-cycle it is. for example, if a motor had only two poles,
     one mechanical revolution would be equal to one electrical revolution, or phase. if a motor has four poles, it would make two electric
     revolutions per complete mechanical revolution, etc. high torque motors tend to have high pole counts (and high speed motors, low pole counts)
  */
  float _ptermsin = ftSin(_theta);
  float _ptermcos = ftCos(_theta);
  // d current, q current at-this-time is
  float _id = _ia * _ptermcos + _ib * _ptermsin;
  float _iq = _ib * _ptermcos - _ia * _ptermsin;

  /*
     then we do PID control
     we want all of the torque on the 'quadrature' axis, the Q axis. 
     because we've done this in a DQ frame, which rotates along with the rotor, we've abstracted away the complications of rotating target-vectors
     and we can write a PI control loop that will use a Voltage Output to control the current flowing through the phases.
  */
  float _id_ref = 0.0;            // target values
  float _iq_ref = 1.0;            // 1 amp on the quadrature axis

  float _id_err = _id_ref - _id;  // error -> how far, currently, are we from the target?
  _id_err_int_rb->push(_id_err);  // adding this error to the integral ring buffer, where we keep our past mistakes (haha)
  float _iq_err = _iq_ref - _iq;
  _iq_err_int_rb->push(_iq_err);

  float _id_err_int;
  _id_err_int_rb->sum(&_id_err_int);  // summing the past errors -> this is just a super simple way of 'integrating' over some chunk of the controller's history.
  float _iq_err_int;
  _iq_err_int_rb->sum(&_iq_err_int);

  float _id_term_p = _id_err * KP_D;        // KP and KI (one for each axis) are somewhat 'arbitrary' values... as in, no hard and fast units.
  float _id_term_int = _id_err_int * KI_D;  // technically they are like 'volts (of control output) per amp (of error) - but in reality these just get the heck tuned out of them until they work.
  float _iq_term_p = _iq_err * KP_Q;
  float _iq_term_int = _iq_err_int * KI_Q;

  float _comm_mag_int = abs(_id_term_int) + abs(_iq_term_int); // then we limit the total I-term output, so that we avoid runaway conditions where the controller decides that it's time to blow some fets
  if(_comm_mag_int > K_LIMIT_INT){
    _id_term_int = _id_term_int * K_LIMIT_INT / _comm_mag_int;
    _iq_term_int = _iq_term_int * K_LIMIT_INT / _comm_mag_int;
  }

  float _vd_comm = _id_term_p + _id_term_int;
  float _vq_comm = _iq_term_p + _iq_term_int;

  float _comm_mag_total = abs(_vd_comm) + abs(_vq_comm); //sqrt(_vd_comm * _vd_comm + _vq_comm * _vq_comm); // limit total control output, as above, no blown electronics please
  if (_comm_mag_total > K_LIMIT_TOTAL) {
    _vd_comm = _vd_comm * K_LIMIT_TOTAL / _comm_mag_total;
    _vq_comm = _vq_comm * K_LIMIT_TOTAL / _comm_mag_total;
  }

  /*
    coming back to ground-truth reality, we bring the rotating-frame vector back into static-frame AB space.
    notice I am using the previously-computed sin and cos terms
  */
  float va = _vd_comm * _ptermcos - _vq_comm * _ptermsin;
  float vb = _vd_comm * _ptermsin + _vq_comm * _ptermcos;

  /*
     and right on the metal, here we are taking these AB terms and plotting them back to the three phases, UVW
  */
  float vu = va;
  float vv = THREE_OVER_TWO * (SQRT_THREE_OVER_THREE * vb - va / 3.0);
  float vw = THREE_OVER_TWO * (-SQRT_THREE_OVER_THREE * vb - va / 3.0);

  /*
   * and writing those values to the PWM registers. notice we're 'normalizing' vu, vv, vw, to -1 -> 1, whereas previously they represented 'real' voltages
   */
  uint16_t vpwmu_hi = 1024 + 1024 * ( vu / V_BUS );
  uint16_t vpwmv_hi = 1024 + 1024 * ( vv / V_BUS );
  uint16_t vpwmw_hi = 1024 + 1024 * ( vw / V_BUS );

  t3pwm->setPhases(vpwmu_hi, vpwmv_hi, vpwmw_hi);

  /*
     END OF LOOP
  */

  /*
   * Reporting and Tracking
   * Using DAC to direct-to-scope current tracking...
   */
  float report = _iq * 2046 + 2048; // range is -1 -> 1
  if(report > 4096){
    report = 4096;
  } else if (report < 1){
    report = 1;
  }
  
  analogWrite(A14, (int)report);
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

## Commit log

2017-06-12 forked from bbesc
    [2017-05-12T12_15_08.csv, bbesc_kiCad.kicad_pcb, bbesc_kiCad.sch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]
2017-07-09 start sampler work, encoder settings discovery script, etc
2017-07-11 add roboscpd, add pwm coordination examples, sketch
2017-07-13 figuring timer registers for pwm and adc coordination
2017-07-14 registers! adc and pwm coordination
2017-07-18 circuit for fab, foc bones
    [bbesc_kiCad-B.Cu.gbr, bbesc_kiCad-B.Mask.gbr, bbesc_kiCad-B.SilkS.gbr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]
2017-07-27 circuit fab files v0.1
    [bbesc_kiCad.kicad_pcb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]
2017-08-18 board v0.2
    [bbesc_kiCad-B.Cu.gbr, bbesc_kiCad-B.Mask.gbr, bbesc_kiCad-B.SilkS.gbr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]
2017-08-26 closed (encoder) loop 'voltage foc' with sinusoid pwm (discovered svpwm errors)
    [_saved_bbesc_kiCad.sch]
2017-08-27 rolling first PI loop :|
    [_saved_bbesc_kiCad.sch, bbesc_kiCad.sch]
